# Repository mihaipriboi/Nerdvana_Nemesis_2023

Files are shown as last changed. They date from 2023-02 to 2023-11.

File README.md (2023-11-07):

<center><h1> Nerdvana Nemesis 2023 </center>

## Table of Contents
* [Photos](#team-image)
  * [Team](#team-image)
  * [Robot](#robot-image)
* [Performance Video](#video)
* [Mobility Management](#mobility-management)
  * [Powertrain](#powertrain-mechanical)
    * [Drivetrain](#drivetrain-mechanical)
    * [Motor](#motor-mechanical)
    * [Motor Driver](#motor-driver-mechanical)
  * [Steering](#steering-mechanical)
    * [Servo Motor](#servo-motor)
  * [Chassis](#chassis-mechanical)
* [Power and Sense Management](#power-and-sense-management)
  * [Li-Po Battery](#li-po-battery)
  * [Teensy 4.1](#teensy-4.1)
  * [LIDAR](#lidar-sensor)
  * [IMU](#imu-sensor)
  * [Pixycam 2.1](#pixy-cam-2.1)
  * [Voltage Regulator](#voltage-regulator-(L7805CV))
  * [Circuit Diagram](#circuit-diagram)
* [Code for each component](#code-for-each-component)
  * [Drive Motor](#drive-motor-code)
  * [Servo Motor](#servo-motor-code)
  * [Camera](#camera-code)
  * [LIDAR](#lidar-code)
    * [Python Data Visualization](#python-data-visualization)
  * [IMU](#gyro-sensor-code)
  * [SD Card](#sd-card-code)
* [Obstacle Management](#obstacle-management)
  * [Qualification Round](#quali-management)
  * [Final Round](#final-management)
* [Randomizer](#randomizer)
* [Resources](#resources)
  * [3D Models](#3d-models-resources)
  * [Images](#images-resources)

### Team: Priboi Mihai, Onișoru Antonia, Bălan Teodor 
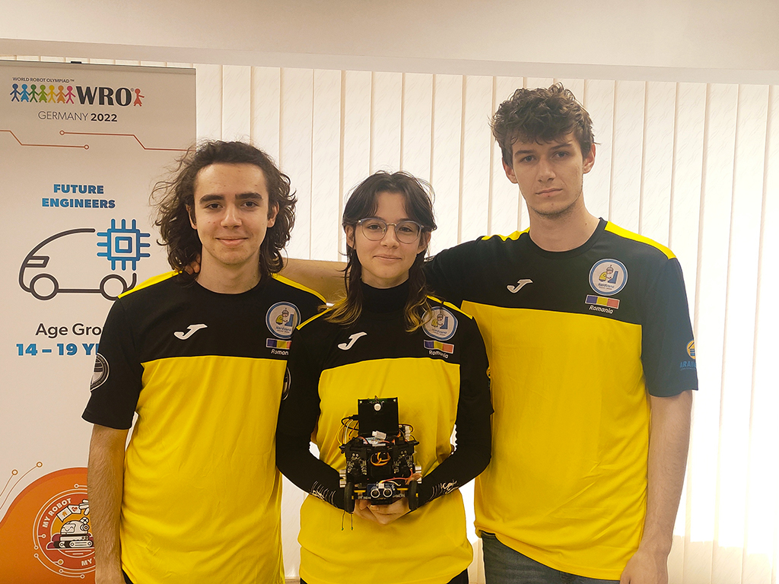
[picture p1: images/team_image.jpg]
Team
  

## Photos of our robot Paula Mia (**P**retty **A**wesome **U**ltra **L**ocomotion **A**utonomous **M**apping **I**ntelligence **A**ugmentation) 

|  |  | 
| :--: | :--: |
| *Front* | *Back* |
|  |  | 
| *Left* | *Right* |
|  |  | 
| *Top* | *Bottom* |

<br>

## Our video of the robot on [Youtube](https://youtu.be/1fn3-xTy-k4) 

<br>

# Mobility Management 
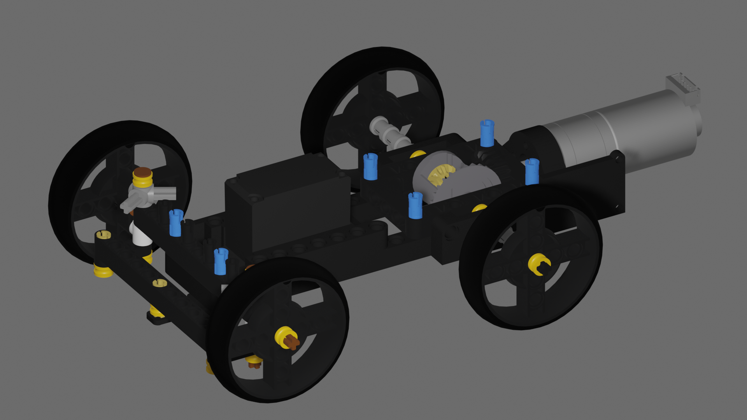
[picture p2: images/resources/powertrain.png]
Powertrain


## Powertrain 

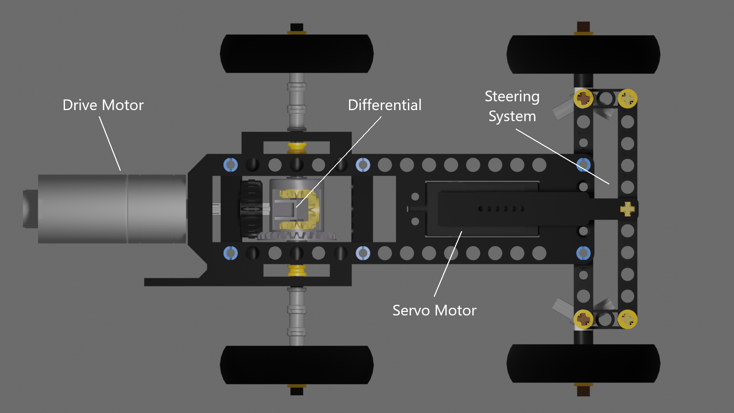
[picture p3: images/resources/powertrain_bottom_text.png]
Powertrain - Bottom View


### Drivetrain 

After reflecting on our experience from last year's competition, where we utilized a rear-wheel drive (RWD) with a differential, we opted for an all-wheel drive (AWD) system for this year's national event. We were motivated to switch because the RWD struggled with steering due to the lack of power in the front wheels. Moreover, an AWD system ensures a more even distribution of power.

However, after deciding to incorporate a LIDAR sensor, we found it essential to mount the sensor low to improve its accuracy. Given its considerable size, and the space constraints for the front differential and driveshaft—further challenged by our decision to place the servo lower to make room for the LIDAR—we ultimately returned to the RWD configuration.

To minimize friction and thereby reduce speed loss, we avoided using 3D-printed components for the moving parts in the drivetrain. Instead, we utilized Lego pieces, which are molded with high precision and therefore have a very low friction coefficient. The 3D-printed parts were reserved for the chassis and for mounting the electronic components onto the Lego structure.

### Motor 

Following an evaluation of different motors, we settled on a geared DC motor that comes with a magnetic encoder. This motor was selected for its lightweight and compact design, which stands out among others with comparable output. Additionally, the magnetic encoder offers greater precision than its optical counterpart. We secured the motor to the chassis using screws.

**Specifications:**
- Voltage: < 7V
- Gear Ratio: 1:20
- Speed: 400 ± 13% rpm
- Torque: 0.4 ± kg·cm
- Weight: 67.4g

Where to buy the motor: https://www.adafruit.com/product/4416

To connect the motor's axle to a Lego-compatible axle, we created a custom 3D-printed adapter.

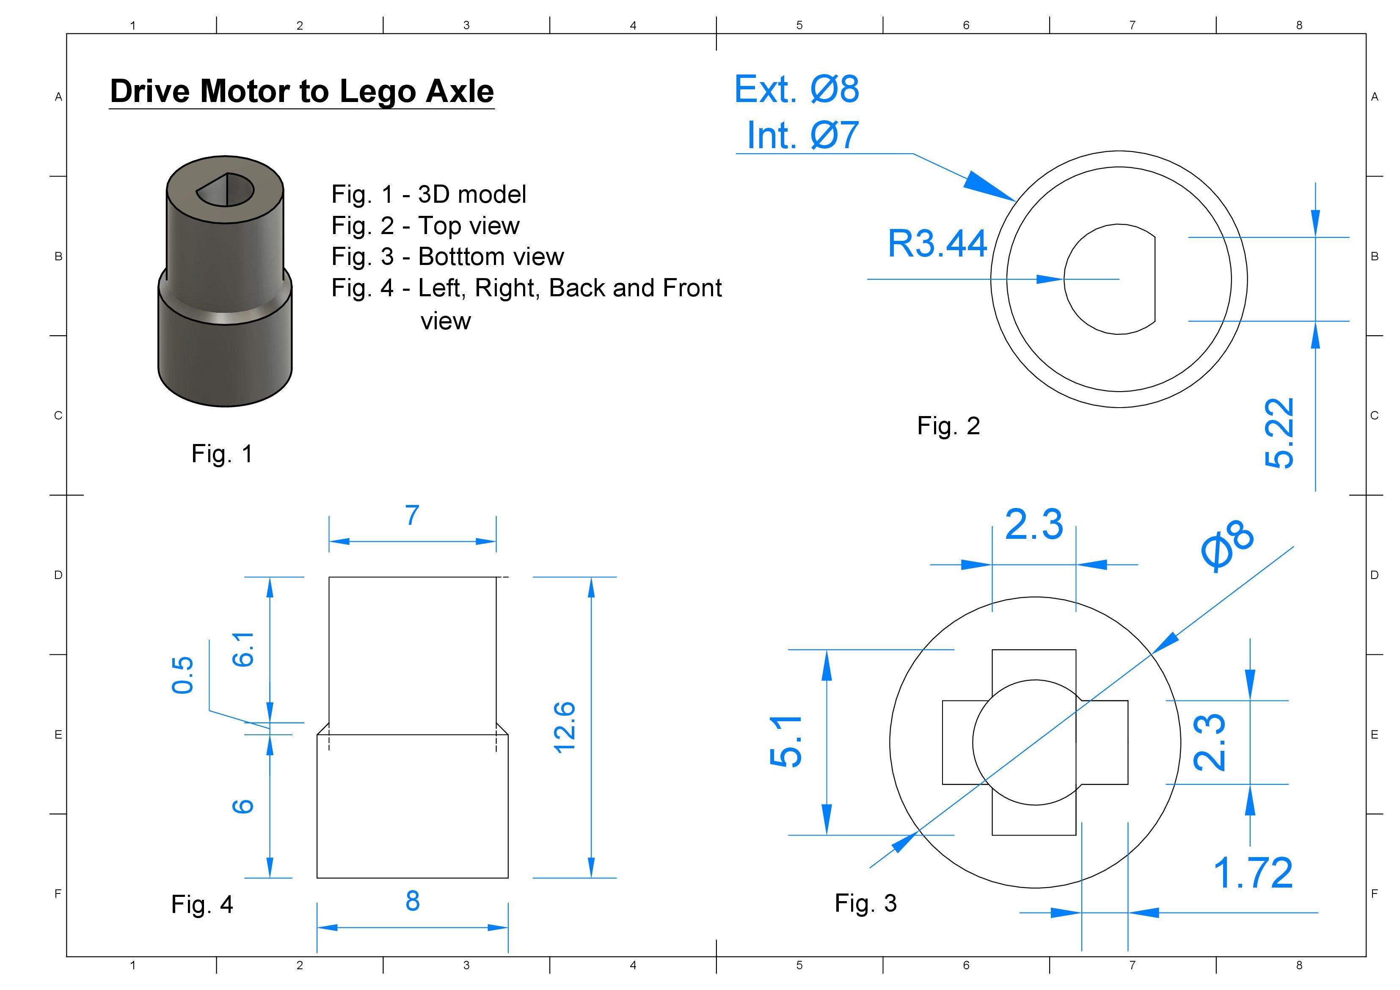
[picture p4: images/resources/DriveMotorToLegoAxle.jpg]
Gearmotor to axle - 3D Model Gearmotor to axle 3D piece


### Motor Driver 
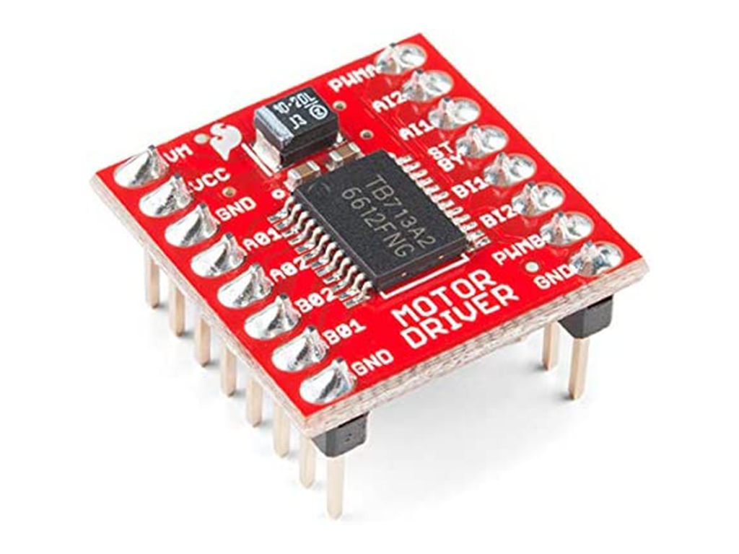
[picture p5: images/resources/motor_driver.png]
Motor driver


To control the speed of the drive motor, we utilized a SparkFun Dual TB6612FNG motor driver.

Where to buy the motor driver: https://www.sparkfun.com/products/14450

## Steering 

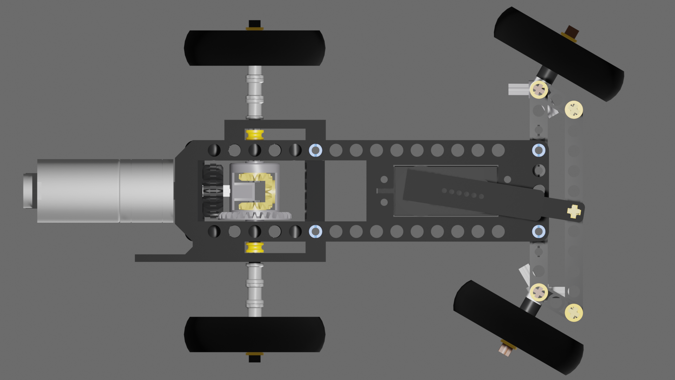
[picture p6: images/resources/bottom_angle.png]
Powertrain - Angled Bottom View


After experimenting with various steering mechanisms such as Ackermann steering and bell-crank steering, we assessed their advantages and drawbacks. Ultimately, we chose a straightforward steering system consisting of a parallelogram linkage. This decision was made because the alternative systems were either too large or too complex to implement effectively. Our selected mechanism is simple, light, and compact, providing a satisfactory steering angle. While it does not adhere to the Ackermann steering geometry, our tests showed that for our robot's small size and light weight, this omission was not critically significant.

### Servo Motor 
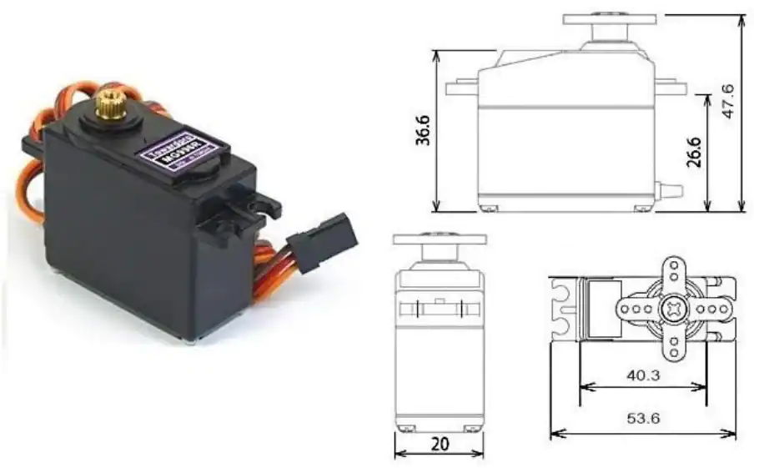
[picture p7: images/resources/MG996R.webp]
MG996R Servo


For steering, we selected the MG996R servo motor, favoring it for its high torque and swift response.

**Specifications:**
- Weight: 55g
- Stall torque: 9.4 kg/cm (4.8v)
- Operating speed: 0.17 s/60 degree (4.8v)
- Rotation angle: 180 degree

Where to buy the servo motor: https://www.sigmanortec.ro/servomotor-mg996r-180-13kg

To connect the servo motor to the steering system, we fashioned a custom 3D-printed adapter. Given the dynamic geometry of the system, the connector couldn't be a single rigid piece because its length needed to be adjustable according to the wheel positions. Thus, we designed a two-part beam: the larger piece attaches to the servo and the smaller piece to the steering mechanism. The smaller piece slides into the larger one, permitting the beam's length to vary. We introduced a slight space between the two components to ensure smooth movement, while also ensuring that a significant portion of the smaller piece remains within the larger one to avoid disconnection or bending.

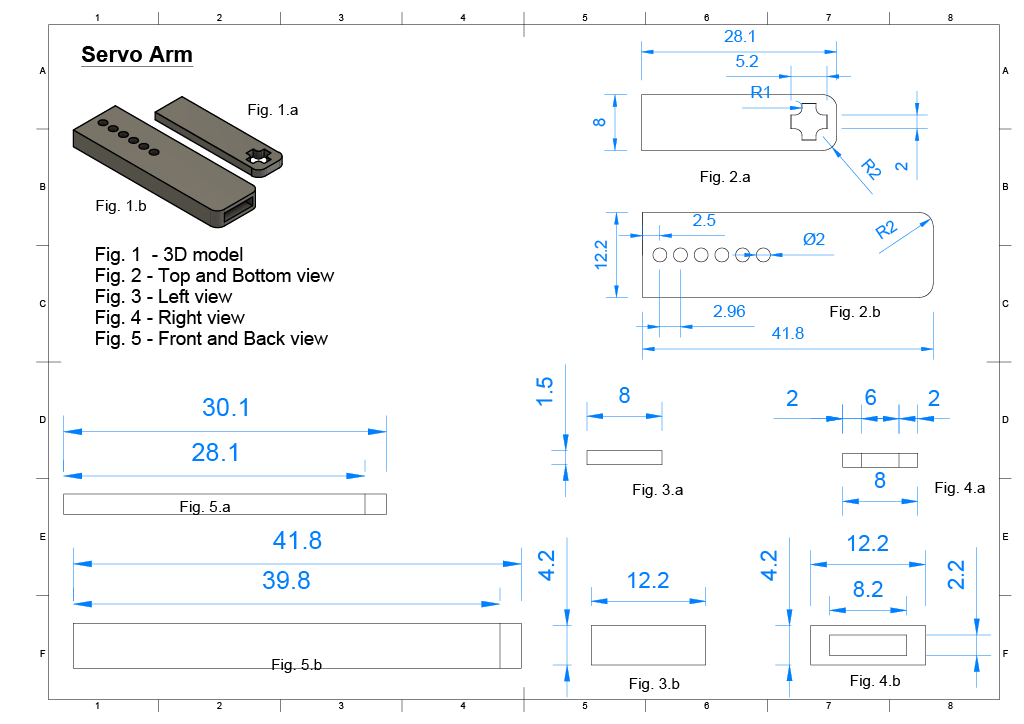
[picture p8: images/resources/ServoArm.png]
Servo Arm - 3D Model Servo Arm


## Chassis 

Our initial prototypes utilized Lego pieces to assemble all components, which simplified testing and design modifications. Once we finalized the design, we transitioned to a custom 3D-printed chassis for assembling the mechanical parts. This choice proved to be superior, resulting in a lighter and more compact structure that offered greater design flexibility compared to the Lego-based framework. The chassis accommodates the drivetrain and steering mechanism and includes designated mounts for securing the drive motor and servo motor.

Incorporating a LIDAR system necessitated maintaining all components, except for the LIDAR itself, below a certain height (approximately 8 cm, slightly less than the wall height) to ensure an unobstructed field of view for the sensor. Consequently, we had to extend the robot's length more than preferred, but this was an essential compromise. The drive motor extends out from the back of the robot, while the servo motor is centrally positioned directly beneath the LIDAR. Due to spatial constraints preventing the servo motor from being placed higher, we relinquished the all-wheel drive in favor of an alternative configuration. The gyroscope sensor is also mounted on the chassis, positioned near the drive motor.

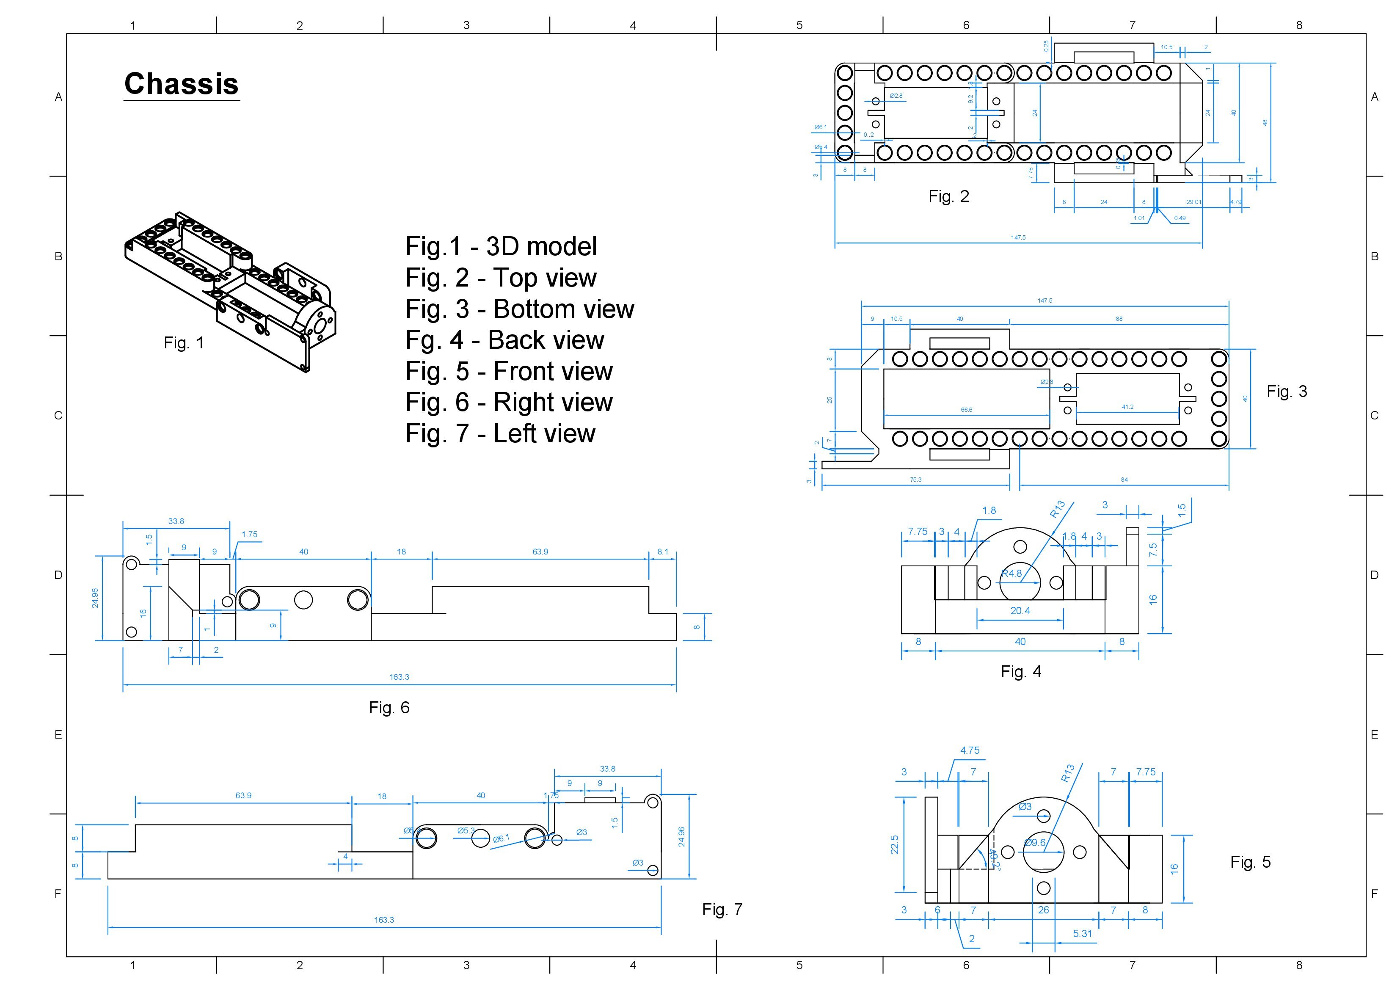
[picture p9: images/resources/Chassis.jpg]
Chassis - 3D Model


# Power and Sense Management 

### Li-Po Battery 
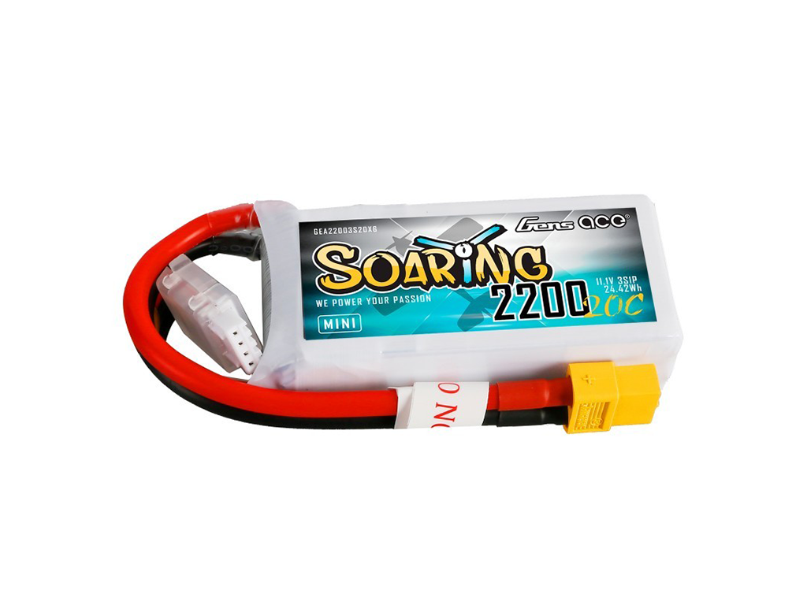
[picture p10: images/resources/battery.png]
Li-Po Battery


Last year, we powered our robot with a 6-pack of AA Nickel-Metal Hydride (NiMH) batteries, which provided approximately 7.2V and 2000mAh but weighed around 650g. With our goal of building a smaller and lighter robot, we recognized the need for a different power source. We chose a Lithium Polymer (Li-Po) battery for its lighter weight, more compact size, and quicker charging capabilities. The specific model we selected is the *LiPo GENS ACE Soaring* (7.4V, 2200mAh, 20C). Switching to this battery reduced the weight of our power pack from 650g to 100g, almost halving the robot's weight. Moreover, the battery is more than twice as small in terms of volume.

Where to buy the battery: https://www.sierra.ro/Acumulator-LiPo-GENS-ACE-Soaring-7-4-V--2200-mA--20C-p11141p.html

The battery is mounted using a custom 3D-printed holder, which is secured to the chassis.

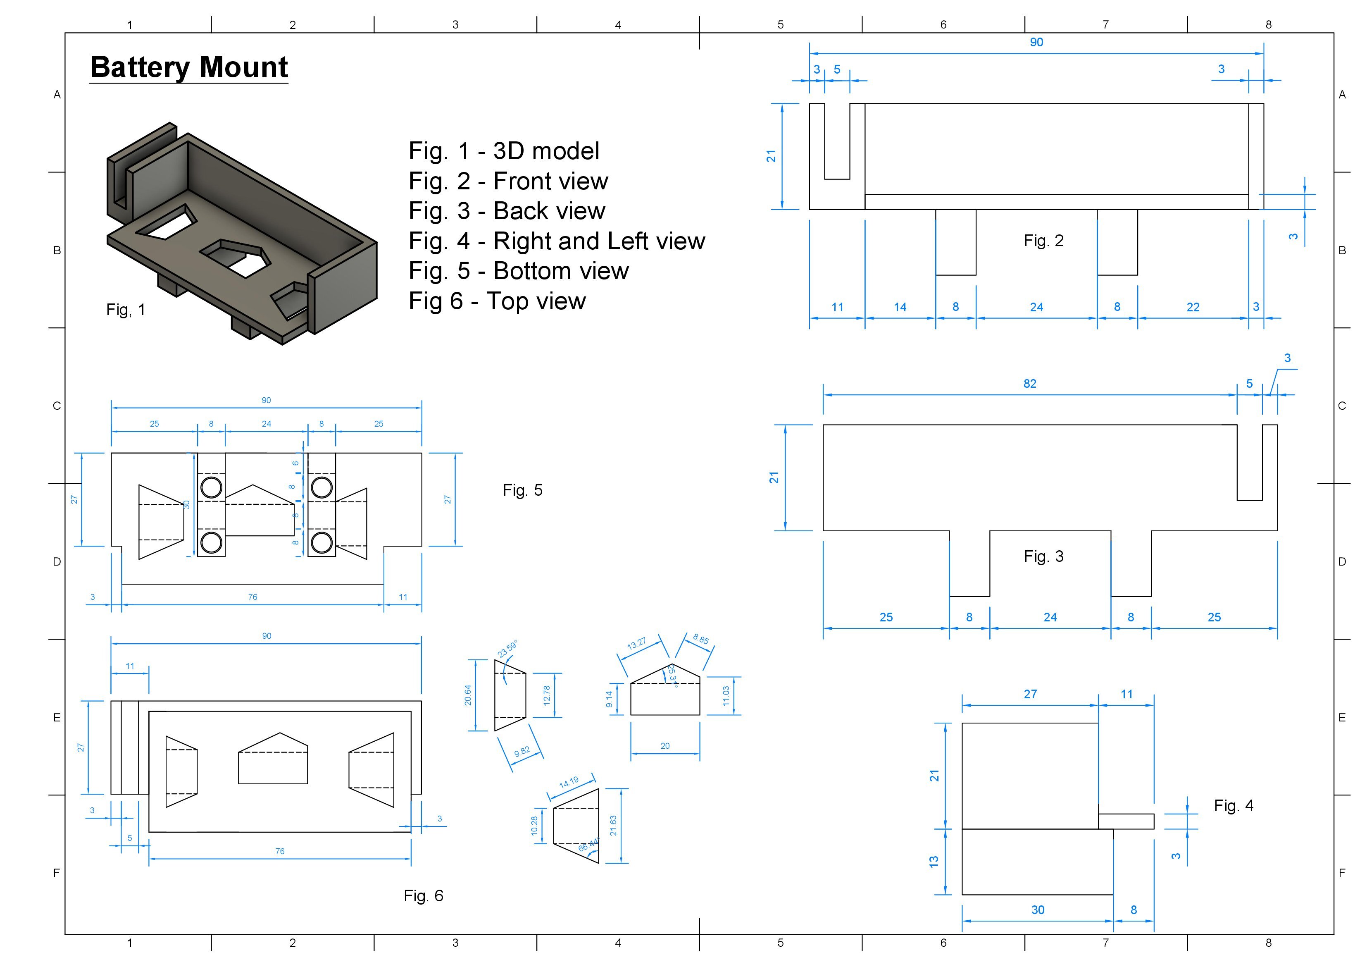
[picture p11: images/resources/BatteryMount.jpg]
Battery Mount - 3D Model


### Teensy 4.1 
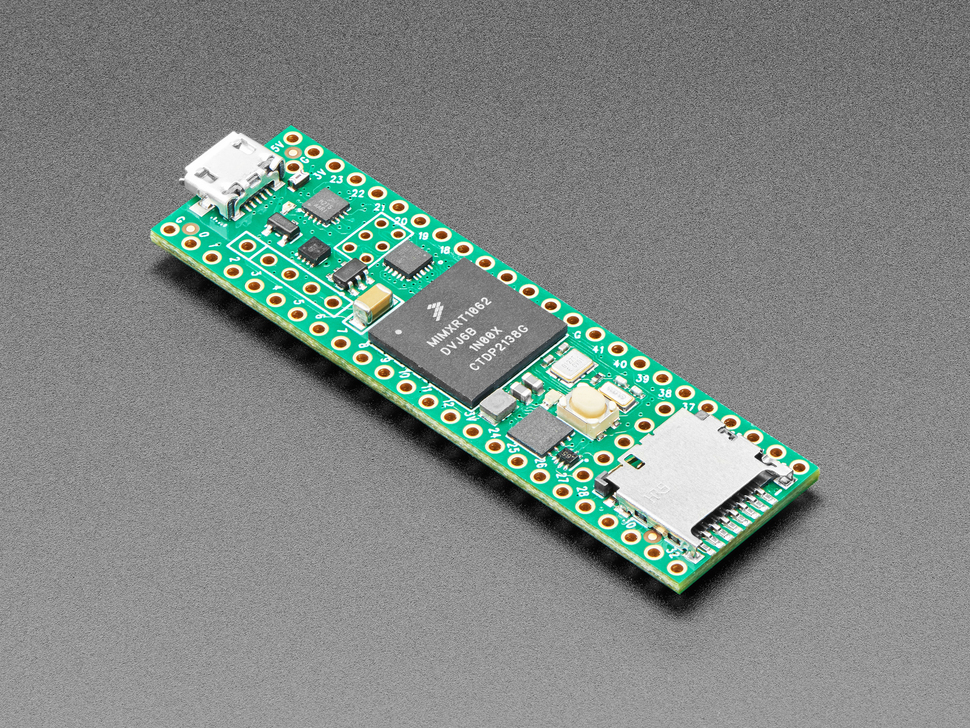
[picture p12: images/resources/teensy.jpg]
Teensy 4.1 Teensy 4.1


At WRO2022 Future Engineers, we used a Raspberry Pi 3B+ in conjunction with an Arduino Uno Every through a serial connection. The Raspberry Pi was tasked with processing images from the camera, whereas the Arduino was dedicated to controlling the motors and collecting sensor data. This method, however, was not optimal. The processing speed of the Raspberry Pi fell short of our requirements, the serial link between the two boards was not as quick as necessary, and it also carried the risk of data loss.

Following the international competition in Dortmund, we discovered the Pixycam 2.1, a camera equipped with its own processing capabilities that can directly connect to an Arduino or other microcontrollers. With the Pixycam 2.1, we were able to remove the Raspberry Pi, thereby enhancing our robot's speed. We also upgraded from the Arduino Uno Every to a Teensy 4.1, which boasts much faster processing power.

| Specification | Arduino Nano Evey | Teensy 4.1 |
| :--: | :--: | :--: |
| Clock Speed | 20MHz | 600 MHz |
| CPU Flash Memory | 48 KB | 8 Mbytes |
| CPU RAM | 6 KB | 1 MB |
| Digital I/O Pins | 20 | 42 |
| PWM Pins | 7 | 14 |
| UART | 1 | 6 |
| SPI | 1 | 3 |
| I2C | 1 | 3 |

Where to buy the Teensy 4.1: https://www.pjrc.com/store/teensy41.html

The Teensy, mounted on a prototype board, is secured to the chassis with a custom 3D-printed holder.

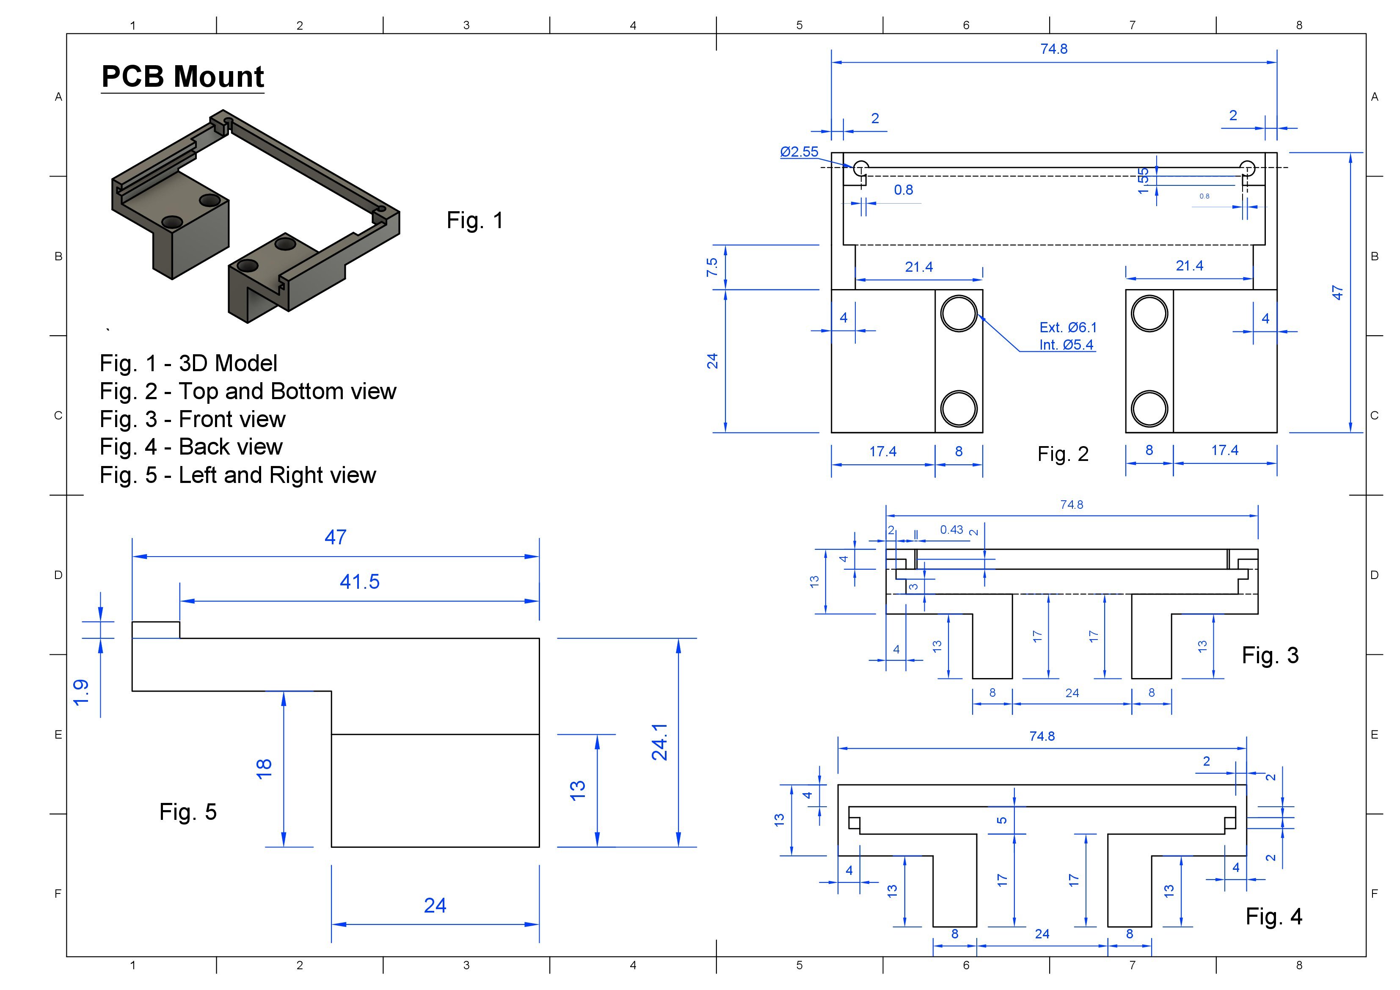
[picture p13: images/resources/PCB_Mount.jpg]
PCB Mount - 3D Model


### LIDAR 
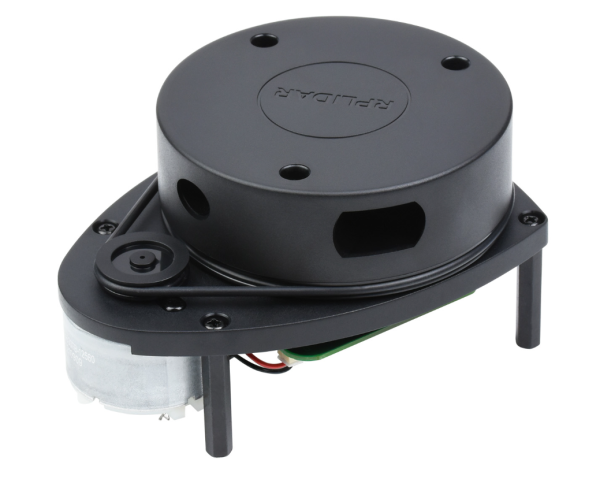
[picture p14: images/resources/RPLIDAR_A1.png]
RPLIDAR A1


The LIDAR A1 sensor is a crucial component of our robot. It provides the robot with a 360° view of its surroundings, allowing it to detect obstacles and avoid collisions. We selected the RPLIDAR A1, which is a low-cost LIDAR system that offers a 360° scan at a frequency of 10Hz. The sensor is equipped with a 2D laser scanner that can detect objects up to 8 meters away. The sensor is wired to the Teensy 4.1 via the SDA and SCL pins.

In the lead-up to the World Robot Olympiad (WRO) 2022, an iterative process of solution development was undertaken, aiming to resolve the persistent challenge of precise robot localization and obstacle detection under variable environmental conditions. The trials encompassed the deployment of both ultrasonic and infrared sensors. However, these sensors exhibited limitations in terms of angular sensitivity and dependability, influenced by the robot's orientation, which impeded their effectiveness for consistent environmental navigation and recognition tasks.

Where to buy the RPLIDAR A1: https://www.adafruit.com/product/4010

The LIDAR is secured to the chassis with custom 3D-printed holders on each leg.

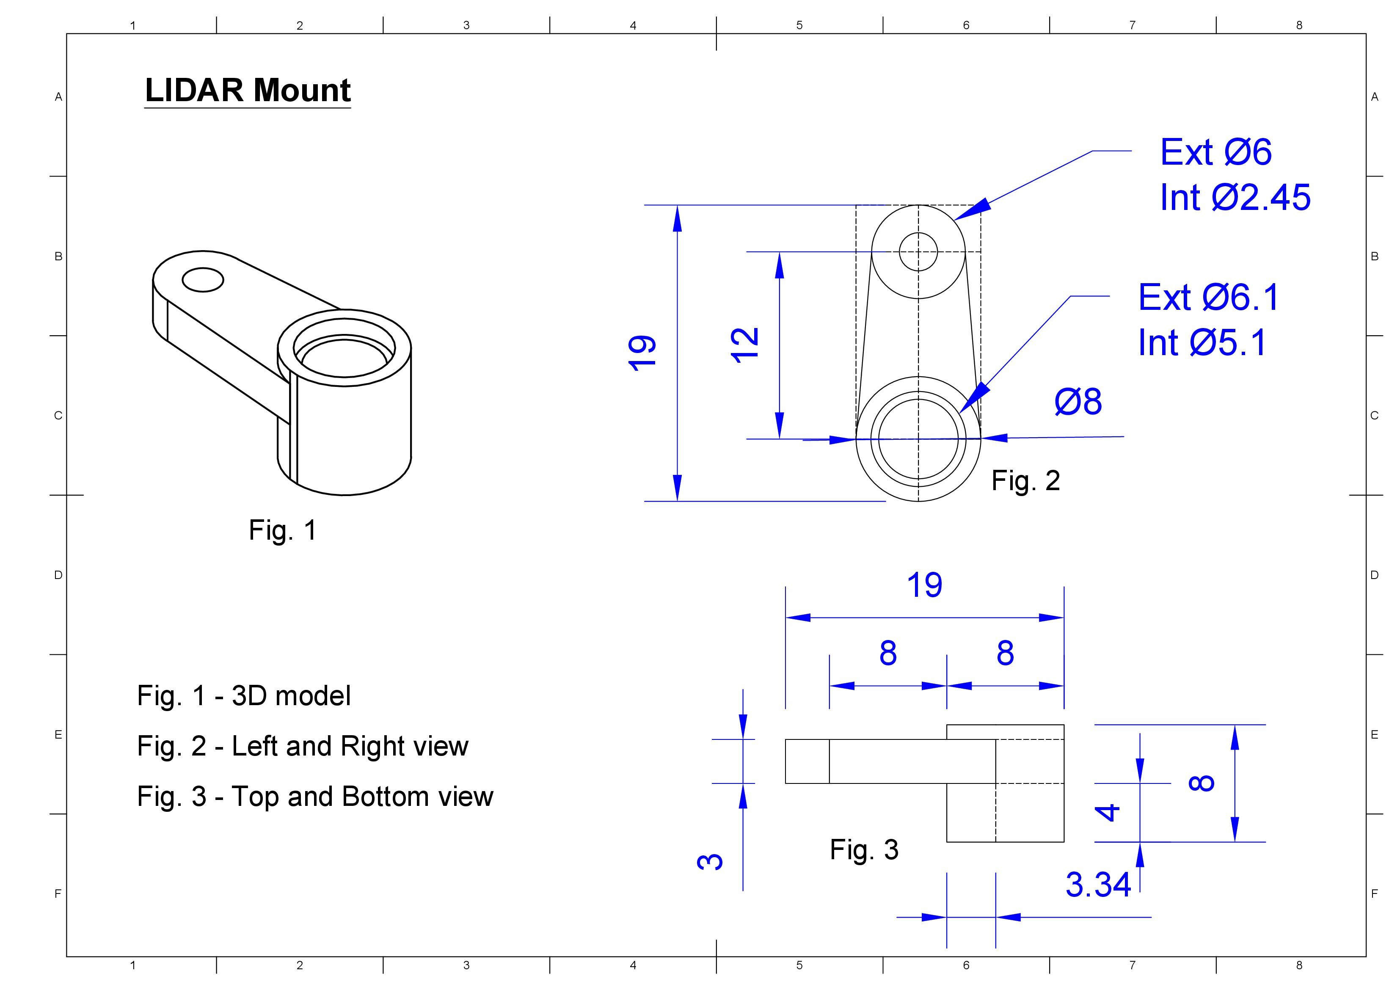
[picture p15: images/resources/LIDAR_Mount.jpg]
LIDAR Mount - 3D Model


### IMU 
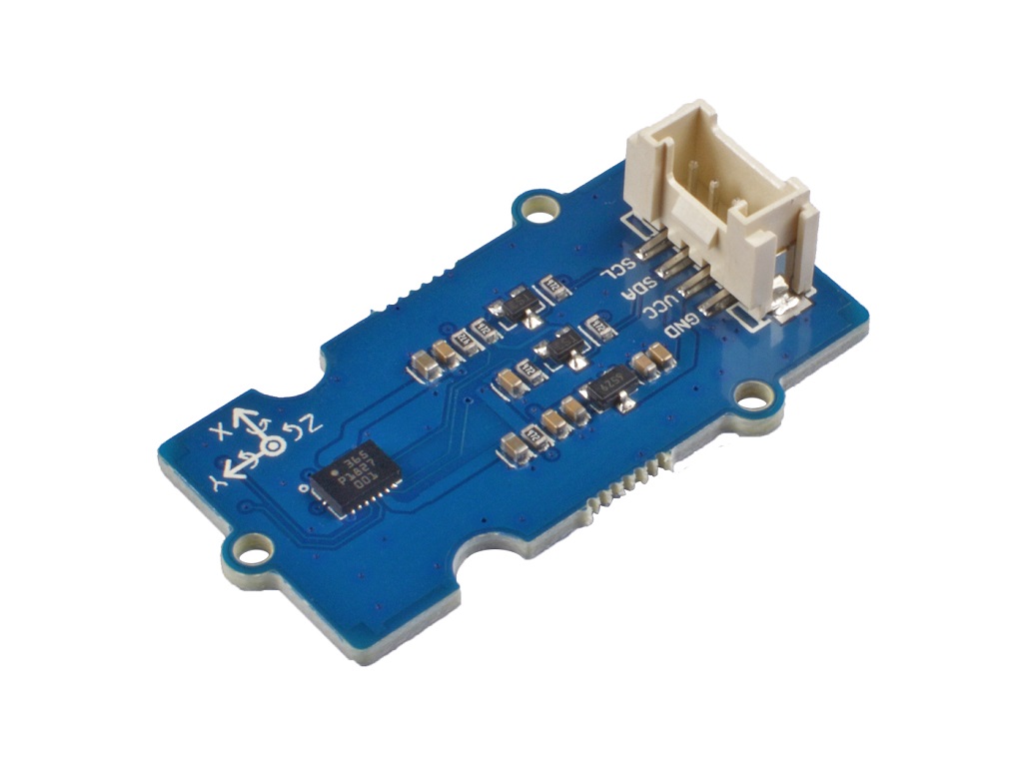
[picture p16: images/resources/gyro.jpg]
IMU Sensor - BMI088


One importat aspect that helps the roboy navigate is the inertial measurement unit (IMU). After using the MPU6050 last year, we decided to upgrade to a better IMU. This sensor is based on BOSCH BMI088, which is a high-performance IMU with high vibration suppression. While the IMU measure the angular velocity and the acceleration of the robot, we only use the angular velocity to calculate the angle of the robot. The IMU is wired to the SDA and SCL pins on the teensy.

**Specifications:**
- Gyroscope range: ±2000°/s
- Accelerometer range: ±24g

Where to buy the gyro sensor: https://www.seeedstudio.com/Grove-6-Axis-Accelerometer-Gyroscope-BMI088.html

### Pixycam 2.1 
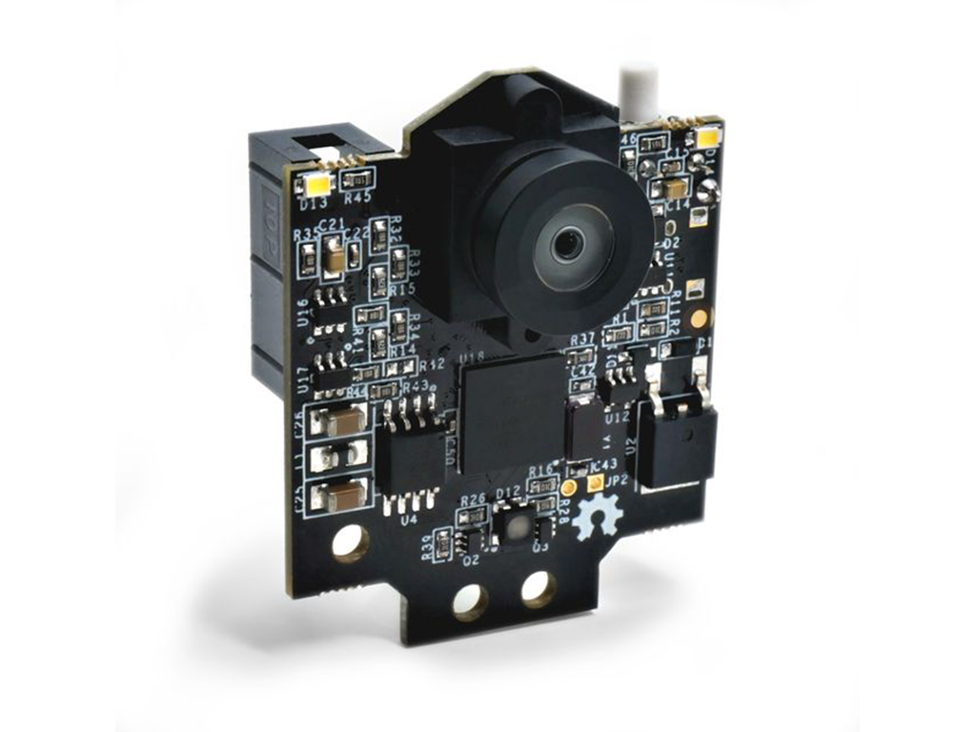
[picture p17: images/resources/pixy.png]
Pixycam 2.1


Last year, one of our main challenges was the slow speed of the camera feed. We were utilizing a Raspberry Pi equipped with a PiCam V2. The delay was primarily due to the need to run a cube recognition machine learning algorithm on the Raspberry Pi itself, which limited the processed image feed to around 15 frames per second. This not only reduced the camera's efficiency but also slowed down the processing of other tasks on the Raspberry Pi.

To address this, we switched to the Pixycam 2.1, which offers several significant benefits: it possesses its own processing unit, thus preventing any lag in the rest of the system; it comes with a professionally developed machine learning algorithm for object detection and tracking, which performs reliably; and it can directly interface with an Arduino or another microcontroller, eliminating the need for a Raspberry Pi and so increasing the frequency of the readings.

Together with the Teensy 4.1, the camera delivers readings at approximately 60 frames per second, a limit we've set ourselves. Additionally, the camera's operation doesn't impact the performance of other sensors, allowing us to take full advantage of their capabilities.

Where to buy the PixyCam 2.1: https://www.robotshop.com/products/charmed-labs-pixy2-robot-vision-image-sensor-lego-rbc

The Pixycam 2.1 is mounted on the chassis with a custom 3D-printed holder.

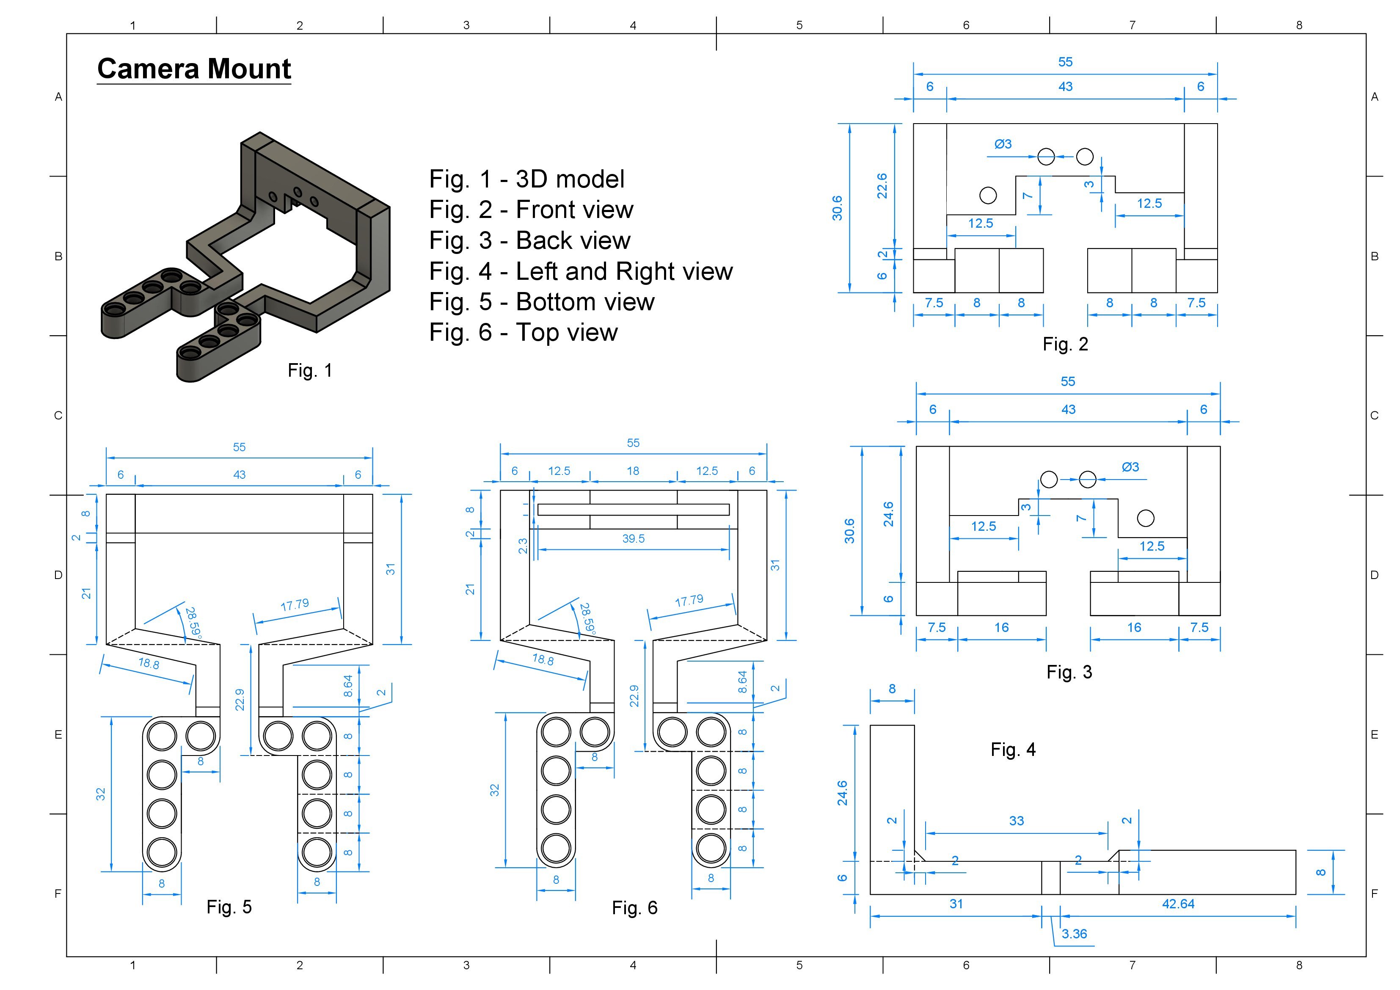
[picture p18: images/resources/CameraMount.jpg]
Pixycam Mount - 3D Model


### Voltage regulator 
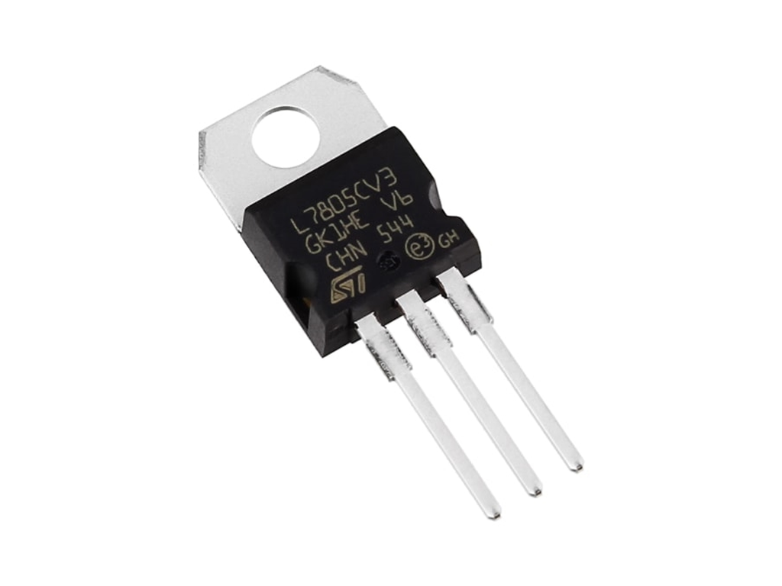
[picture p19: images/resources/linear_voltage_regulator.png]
Voltage regulator (L7805CV)


To provide the Teensy 4.1 with the required 5V, we needed to decrease the output from the 7.4V battery, which can reach up to 8.4V when fully charged. We employed a linear voltage regulator, the L7805CV, capable of converting input voltages below 35V down to a steady 5V.

For the drive motor, which we want to operate at higher speeds, we use a separate voltage regulator, the L7806CV, to step down the battery's 7.4V to 6V. This approach allows us to extract more speed from the motor while maintaining consistent performance across different battery charge levels.

Where to buy the 5V voltage regulator: https://ro.mouser.com/ProductDetail/STMicroelectronics/L7805CV?qs=9NrABl3fj%2FqplZAHiYUxWg%3D%3D

Where to buy the 6V voltage regulator: https://ro.mouser.com/ProductDetail/STMicroelectronics/L7806CV?qs=K4DpzJ20gDEC%252BHE13eVUwg%3D%3D

### Circuit diagram 
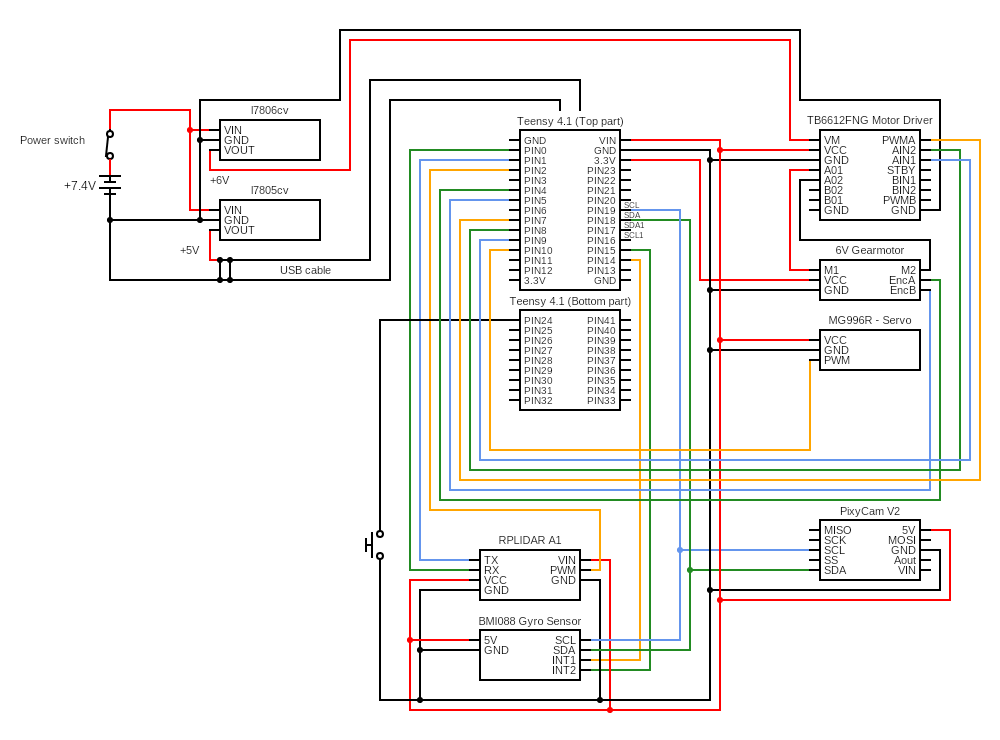
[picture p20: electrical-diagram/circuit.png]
Circuit diagram


<br>

# Code for each component 

## Drive Motor 

The motor driver can be directly managed with a single PWM pin that adjusts the motor's speed and two digital pins designated for determining the motor's rotation direction. Consequently, the use of any external library for motor manipulation was unnecessary.

We devised two functions within our control system: one to modify the motor's velocity and another to halt it effectively, incorporating a braking feature. To achieve this, we convert the desired speed from our established scale of -100 to +100 to the PWM equivalent of 0 to 255. The motor's direction is then adjusted according to the sign of the input value.

```ino
void motor_start(int speed) {
  speed = -speed;  
  int out = abs(speed) * 2.55; // Convert speed to PWM value (0 to 255)
  if(speed >= 0) { // Forward direction
    digitalWrite(AIN1, HIGH);
    digitalWrite(AIN2, LOW);
  }
  else { // Reverse direction
    digitalWrite(AIN1, LOW);
    digitalWrite(AIN2, HIGH);
  }
  analogWrite(PWM1, out);

  Serial << "speed: " << speed << "\n";
}

void motor_stop() {
  motor_start(-10); 
}
```

However, for the encoder, we required a specialized library to handle the more complex signal processing. The library we use for interfacing with the encoder is called *Encoder.h*.

The encoder operates with a straightforward function that we found easy to comprehend and program. The constant with which we multiply the encoder's output value was determined empirically through multiple tests with varying distances. This calibration process allowed us to accurately convert the encoder's readings into centimeters.

```ino
long read_motor_encoder() {
  return (0.01285) * (double)myEnc.read();
}
```

## Servo Motor 

For controlling the servo motor, we utilize the *Servo.h* library, which provides the necessary functions to manage the servo's movements. Initially, we configure the servo by establishing its range, defining the maximum and minimum angles it can achieve in both directions. This ensures that we can accurately position the servo within its operational limits.

```ino
// Servo
void servo_setup() {
  servo.attach(SERVO_PIN, 1400, 1611);
  move_servo(0);
  delay(50);
}
```

The function *move_servo* makes the servo to rotate a specific angle, given by the parameter _angle_. If the angle is negativ the motor will rotate to the left, and if is pozitiv the motor will rotate to right. This way 0 is going to be the position, in which the wheels are straight. Also, the values we are giving the motor need to be between -1 and 1, so we use a clamp function to limit the value we are going to give the motor to roatate to.

```ino
void move_servo(double angle) {
  angle = clamp(angle + servo_correction, -1, 1);

  double angle_deg = 90 + angle * 90.0;  // Convert angle to degrees (0 to 180)
  angle_deg = clamp(angle_deg, 0, 180);
  servo.write(angle_deg);
}
```

## Camera 

Now that we finished to implement the functions we need to make the robot move and steer, we have to make him see the cubes and move according to them. The library we used for the camera is _Pixy2I2C.h_. The I2C address must be configured in the _Pixy2I2C.h_ library.

```ino
void camera_setup(bool debug) {
  if (debug) Serial.println(F("Camera starting..."));
  //display_print("Cam err!");
  pixy.init(0x54);
  if (debug) Serial.println(F("Camera ok!"));

  pixy.getResolution();
  image_w = pixy.frameWidth;
  image_h = pixy.frameHeight;
  // Serial << image_w << " " << image_h << '\n';
}
```

In order to read the inputs from the camera, we have some methods from the Pixy2I2C class.

```ino
pixy.ccc.blocks[i].m_signature
// The signature number of the detected object
// For us, 1 is for red, and 2 is for green
pixy.ccc.blocks[i].m_x
// The x location of the center of the detected object (0 to 316)
pixy.ccc.blocks[i].m_y
// The y location of the center of the detected object (0 to 208)
pixy.ccc.blocks[i].m_width
// The width of the detected object (1 to 316)
pixy.ccc.blocks[i].m_height
// The height of the detected object (1 to 208)
pixy.ccc.blocks[i].m_indez
// The tracking index of the block
```

For the camera we made a function in which we are reading the color of the cube in front of us.

```ino
void read_camera(bool debug) {
  if (millis() - last_camera_read >= camera_interval) {
    pixy.ccc.getBlocks();

    if(pixy.ccc.numBlocks < 1)
      cube_color = 0;
    else
      cube_color = sig_to_col[pixy.ccc.blocks[0].m_signature];

    last_camera_read = millis();
  }
}
```

## LIDAR 

Extracting data from the LIDAR involves processing a continuous stream via Serial1. The lidarRead() function reads bytes one at a time, confirming the correct sequence before storing them in a buffer. Once enough data is gathered, it's processed to inform the robot's navigation. If the buffer is full, the data is saved for later use and the buffer is reset for new data. This method ensures the robot receives reliable information for obstacle detection and avoidance.

```ino
void lidarRead() {
    if (!Serial1.available()) {
        return;
    }
    byte current_byte = Serial1.read();
    if (lidar_buff_ptr == 0) {
        if ((current_byte >> 4) != 0xA) {
            return;
        }
    } else if (lidar_buff_ptr == 1) {
        if ((current_byte >> 4) == 0xA) {
            lidar_buff_ptr = 0;
        } else if ((current_byte >> 4) != 0x5) {
            lidar_buff_ptr = 0;
            return;
        }
    }

    lidar_buff[lidar_buff_ptr++] = current_byte;

    if (lidar_buff_ptr == 4) {
        lidarProcessingData();
    }

    if (lidar_buff_ptr == 84) {
        memcpy(lidar_old_buff, lidar_buff, 84);
        lidar_buff_ptr = 0;
    }
}
```

The lidarProcessingData() function interprets raw LIDAR data to map out the robot's surroundings. It calculates the starting angle of the scan and then iterates over the data to determine distances and angles for various points. These values are then adjusted for the robot's current orientation, converted into X and Y coordinates, and filtered to ignore any out-of-range readings. If the readings are valid, they're processed further to assist the robot in navigation and obstacle avoidance.

```ino
void lidarProcessingData() {

    double start_angle = (((uint16_t)(lidar_buff[3] & 0b01111111) << 8) ^ lidar_buff[2]) / 64.;
    double old_start_angle = (((uint16_t)(lidar_old_buff[3] & 0b01111111) << 8) ^ lidar_old_buff[2]) / 64.;

    for (int i = 0; i < 16; ++i) {
        byte* cabin = lidar_old_buff + 5 * i + 4;
        
        d0[0] = getDiffAngle(((cabin[0] & 0b11) << 4) ^ (cabin[4] & 0b1111));
        d0[1] = getDiffAngle(((cabin[2] & 0b11) << 4) ^ (cabin[4] >> 4));

        for (int i = 0; i < 2; ++i) {
            distance[i] = ((uint16_t)cabin[2 * i + 1] << 6) ^ (cabin[2 * i] >> 2);
        }

        for (int j = 0; j < 2; ++j) {
            int k = 2 * i + 1 + j;
            double angle = old_start_angle + angleDiff(old_start_angle, start_angle) / 32 * k;
            if (angle >= 360) {
                angle -= 360;
            } else if(angle < 0) {
              angle = angle + 360;
            }

            double x, y;

            float gx_angle = fmod((double)(angle + (double)gx - current_angle), 360.0);

            y = -distance[j] * cos(radians(gx_angle));
            x = -distance[j] * sin(radians(gx_angle));

            if(distance[j] > 5 && distance[j] < 4000) {
              lidarProcessPoint(Angle(distance[j], gx_angle), Point(x, y));
            }
        }
    }
}
```

The *calculate_linear_regression_segment* function performs a linear regression analysis on a set of data points from LIDAR readings to determine the linear path that best fits the trajectory of an observed barrier. It computes the line's gradient and intercept, pinpoints the coordinates for the beginning and end of the trajectory, and ascertains the barrier's direction in relation to the robot's orientation. Additionally, this function measures the shortest distance from the robot to the barrier.

Another part of the code accumulates data points into a 'current line' array if they are incrementally consistent in distance and direction with the previously recorded point. When this collection reaches a certain size, or there is a notable shift in the data points' position or angle, it initiates the aforementioned linear regression analysis on the gathered segment. Should the barrier be located at a substantial distance, this detected range is then updated. Special conditions within the function are also set to recognize the contours of a cube, modifying the cube's recorded distances as needed when certain parameters are fulfilled.

```ino
void calculate_linear_regression_segment(Point& start, Point& end, double& dist, int& dir) {  
  if(current_line_size < 2) return; // Not enough points for regression
  
  double x_start = INFINITY, x_end = -INFINITY;
  double x_sum = 0, y_sum = 0, x2_sum = 0, xy_sum = 0;
  for(int i = 0; i < current_line_size; ++i) {
    x_sum += current_line[i].x;
    y_sum += current_line[i].y;
    x2_sum += current_line[i].x * current_line[i].x;
    xy_sum += current_line[i].x * current_line[i].y;

    if(current_line[i].x < x_start) x_start = current_line[i].x;
    if(current_line[i].x > x_end) x_end = current_line[i].x;
  }

  double m, c;

  if(current_line_size * x2_sum - x_sum * x_sum == 0) m = INF;
  else m = (current_line_size * xy_sum - x_sum * y_sum) / (current_line_size * x2_sum - x_sum * x_sum);
  
  c = (y_sum - m * x_sum) / current_line_size;

  start.x = x_start;
  start.y = m * x_start + c;
  
  end.x = x_end;
  end.y = m * x_end + c;

  dist = abs(c) / sqrt(1 + m * m);

  if(abs(m) < 0.4) {
    if((start.y + end.y) / 2 < 0) 
      dir = BACK;
    else 
      dir = FRONT;
  } else {
    if((start.x + end.x) / 2 < 0)  {
      dir = LEFT; 
    }
    else {
      dir = RIGHT;
    }
  }
  slopes[dir] = m;
}

void lidarProcessPoint(Angle angl, Point p) {
  double ang, dist;
  ang = angl.ang;
  dist = angl.dist;

  if(abs(dist - old_dist) < 10 && min(abs(ang - old_ang), 360 - abs(ang - old_ang)) < 1.5) {
    current_line[current_line_size++] = p;
  } else {
      if(current_line_size > calculate_threshold(old_dist)) {
        Point start, end;
        double wall_d;
        int wall_dir;

        calculate_linear_regression_segment(start, end, wall_d, wall_dir);

        if(wall_d > 50) {
          old_wall_dist[wall_dir] = wall_dist[wall_dir];
          wall_dist[wall_dir] = wall_d;
          if(wall_dir == FRONT && (wall_dist[FRONT] + wall_dist[BACK]) < 2800) {
            wall_dist[BACK] = 3050 - wall_d;
          }
          wall_updated[wall_dir] = true;
        }

      }
      else if(current_line_size > 2 && (abs(dist - old_dist) > 20 || 
      abs(ang - old_ang) > 5) && (old_ang > 120 && old_ang < 240) &&
       old_dist < 1000 && old_dist > 100 && (wall_dist[BACK] < 1500 ||
        wall_dist[FRONT] > 1400)) {
        xa = current_line[current_line_size / 2].x;
        ya = current_line[current_line_size / 2].y;

        if(xa && ya && wall_dist[side_wall]) {
          double na = ya - slopes[side_wall] * xa;
          dist_to_cube = (-1) * na / sqrt(slopes[side_wall] * slopes[side_wall] + 1);
          //left
          if(dist_to_cube && !last_dist_to_cube && cube_color && abs(wall_dist[side_wall] + direction * dist_to_cube) < 850) { 
            last_dist_to_cube = dist_to_cube;
            last_cube_y = wall_dist[BACK] + ya;
            if(last_cube_y > 2000)
              last_cube_y = 2000;
            if(last_cube_y < 1000)
              last_cube_y = 1000;
          } 
        }
      }
      current_line_size = 0;
      current_line[current_line_size++] = p;
  }
  old_dist = dist;
  old_ang = ang;
}
```

We found that the number of points defining a line decreases with distance in LIDAR data. To predict this variation, we applied a polynomial model that helps improve our detection and mapping accuracy.

```ino
import numpy as np

data = np.loadtxt('data.csv', delimiter=',')

distances = data[:, 0]
points = data[:, 1]

coefficients = np.polyfit(distances, points, 2)

a, b, c = coefficients

print("Best fit parameters: a =", a, "b =", b, "c =", c)

def polynomial_function(D):
    return a * D**2 + b * D + c

distance = 100
estimated_points = polynomial_function(distance)
print("Estimated points at distance", distance, "cm:", estimated_points)

```

```ino
double calculate_threshold(double distance) {
  distance /= 10.0; 
  double a = 0.0010947040728267199;
  double b = -0.46574727812407213;
  double c = 56.010728111461475;
  double points = a * distance * distance + b * distance + c;
  double threshold = max(7.0, points);  // Ensure threshold is at least 7
  threshold = min(20, threshold);
  return threshold;
}
```

The gyro sensor's measurement of the robot's rotation angle is essential for precise spatial positioning. This angle adjusts the lidar data to reflect true distances, accounting for changes in position and orientation. Neglecting this leads to mapping inaccuracies, hence, rotation compensation is critical for precise navigation.

### Python Data Visualization 

To simplify the configuration process for the LIDAR sensor, we developed a Python script that graphically represents the sensor's data. This script takes the wall segments detected by the LIDAR, illustrates them in a chart, and annotates each with the measured distance from the robot. Below, you'll find a sample visualization generated by this program.

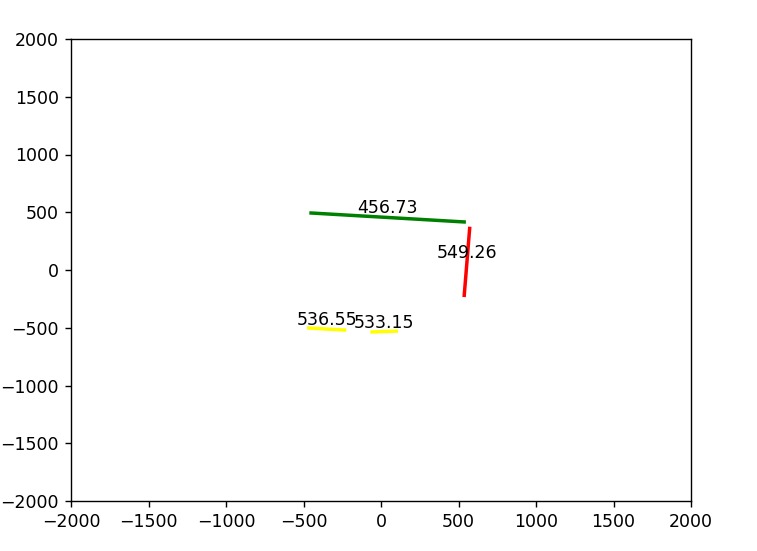
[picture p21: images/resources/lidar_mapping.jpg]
LIDAR Python Mapping


```py
from cmath import cos
from math import radians, sin, sqrt
import math
import matplotlib.pyplot as plt
from collections import deque
import random
import time
import numpy as np
import serial

# Arduino setup
arduino = serial.Serial(port='COM9', baudrate=115200, timeout=.1)

# Create a fixed-length deque of length 50 to store the data points
data_points = deque(maxlen=600000)

# Create an empty plot
fig, ax = plt.subplots()

# Set the x-axis and y-axis limits
ax.set_xlim(-2000, 2000)
ax.set_ylim(-2000, 2000)

# Create a scatter plot to visualize the data points
scatter = ax.scatter([], [])

last_update_time = time.time()

update_interval = 0.5

data = arduino.readline().decode().strip()
old_dist, old_ang = map(float, data.split())

line_counter = 0
colorLines = ['black', 'red', 'blue', 'green', 'yellow', 'orange', 'purple', 'pink', 'brown', 'gray']
colorVec = []

saveLine = []
lines = []
cubes = []

m_left = 0

def calculate_linear_regression_segment(points):
    x, y = points[:, 0], points[:, 1]
    A = np.vstack([x, np.ones_like(x)]).T
    m, c = np.linalg.lstsq(A, y, rcond=None)[0]
    
    # Calculate endpoints of the segment
    x_start = x.min()
    y_start = m * x_start + c
    
    x_end = x.max()
    y_end = m * x_end + c

    dist = abs(c) / np.sqrt(1 + m**2)

    return x_start, y_start, x_end, y_end, m, dist

def plot_segment_with_coefficient(ax, points, order):
    global m_left
    x_start, y_start, x_end, y_end, m, dist = calculate_linear_regression_segment(points)

    color = 'black'
    #black not determined
    #red right
    #blue left
    #green up
    #yellow down

    if(abs(m) < 1): # horizontal line
      if((y_start + y_end) / 2 < 0):
        color = 'yellow'
      else:
        color = 'green'
    else:
      if (x_start + x_end) / 2 < 0:
        color = 'blue'
        m_left = m
      else:
        color = 'red'
       
    ax.plot([x_start, x_end], [y_start, y_end], color=color, linewidth=2)
    # get distnace from origin to the line
    
    ax.text((x_start + x_end) / 2, (y_start + y_end) / 2, f'{round(float(dist), 2)}', 
            horizontalalignment='center', verticalalignment='bottom')

def calculate_threshold(distance):
    distance = distance / 10
    a = 0.0010947040728267199
    b = -0.46574727812407213
    c = 56.010728111461475
    points = a * distance**2 + b * distance + c
    threshold = max(14, points)  # Ensure threshold is at least 14
    threshold = min(20, points)
    return threshold

# Main loop to continuously read and update data
while True:
    data = arduino.readline().decode().strip()
    if data:
        dist, ang = map(float, data.split())
        point_y = -1 * dist * cos(radians(ang));
        point_x = -1 * dist * sin(radians(ang));

        if(old_ang <= 360 and ang >= 0 and old_ang > ang):
           if(len(lines)):  

            for line in ax.lines:
              line.remove()
            for text in ax.texts:
              text.remove()

            order = 0
            for line in lines:
              plot_segment_with_coefficient(ax, line, order)
              order += 1

            if m_left:
              for cube in cubes:
                x1, y1 = cube[0]
                b = y1 - m_left * x1
                y_line = m_left * np.array([x1, x1 - 100]) + b  # x1+10 is just an example, you can choose other values
                dist = -1 * b / sqrt(m_left * m_left + 1)
                ax.plot([x1, x1 - 100], y_line, color="black", linewidth=2)
                ax.text((x1 + x1 - 100) / 2, (y1) / 2, f'{round(float(dist), 2)}', 
                  horizontalalignment='center', verticalalignment='bottom')

            cubes.clear()

            lines = []
            cubes = []
            
            line_counter = 0
            colorVec = []
            pointCnt = 0

            plt.pause(0.00001)
            
        if(abs(dist - old_dist) < 10 and min(abs(ang - old_ang), 360 - abs(ang - old_ang)) < 1.5):
            saveLine.append((point_x, point_y))
        else:
            if(len(saveLine) > calculate_threshold(old_dist)):

              lines.append(np.array(saveLine));
              # save line is a list of tuples

              # data_points.extend(saveLine)
              # colorVec.extend([colorLines[line_counter]] * len(saveLine))
              line_counter += 1
            elif(len(saveLine) > 2 and (abs(dist - old_dist) > 20 or abs(ang - old_ang) > 5) and (old_ang > 130 and old_ang < 240) and old_dist < 800):
               cubes.append(np.array(saveLine));
               data_points.extend(saveLine)
            saveLine.clear()
            saveLine.append((point_x, point_y))

        old_dist = dist
        old_ang = ang

# Show the plot
plt.show()

```

## IMU 

To utilize the gyro sensor, we needed to include the _BMI088.h_ library. During initialization, we allocate a 10-second window to measure the sensor's drift, allowing us to refine the robot's angular readings for greater precision. Additionally, we configure the sensor's output data rate to 400Hz and set the bandwidth to 47Hz. The bandwidth determines the frequency of data sampling by the sensor; a higher bandwidth yields more precise data at the cost of increased power consumption. We also designate pin 15 as an input and attach an interrupt to it, enabling us to capture data from the sensor as soon as it becomes available.

```ino
void gyro_setup(bool debug) {
  int status = accel.begin();
  status = accel.setOdr(Bmi088Accel::ODR_200HZ_BW_80HZ);
  status = accel.pinModeInt1(Bmi088Accel::PUSH_PULL,Bmi088Accel::ACTIVE_HIGH);
  status = accel.mapDrdyInt1(true);

  status = gyro.begin();

  status = gyro.setOdr(Bmi088Gyro::ODR_400HZ_BW_47HZ);
  status = gyro.pinModeInt3(Bmi088Gyro::PUSH_PULL,Bmi088Gyro::ACTIVE_HIGH);
  status = gyro.mapDrdyInt3(true);

  pinMode(15,INPUT);
  attachInterrupt(15,gyro_drdy,RISING);  

  if(status < 0) {
    if(debug) Serial << "BMI Initialization Error!  error: " << status << "\n";
    //init_error = init_gyro_error = true;
  }
  else  {
    // Gyro drift calculation
    if(debug) Serial.println("Starting gyro drift calculation...");

    gx = 0;
    gy = 0;
    gz = 0;

    gyro_last_read_time = millis();

    double start_time = millis();
    while(millis() - start_time < DRIFT_TEST_TIME * 1000) {
      gyro.readSensor();  
      double read_time = millis();
      gx += (gyro.getGyroX_rads() * (read_time - gyro_last_read_time) * 0.001);
      // gy += (bmi.getGyroY_rads() * (read_time - gyro_last_read_time) * 0.001);
      // gz += (bmi.getGyroZ_rads() * (read_time - gyro_last_read_time) * 0.001);

      gyro_last_read_time = read_time;
    }

    drifts_x = gx / DRIFT_TEST_TIME;
    // drifts_y = gy / DRIFT_TEST_TIME;
    // drifts_z = gz / DRIFT_TEST_TIME;

    if(debug) Serial.print("Drift test done!\nx: ");
    if(debug) Serial.print(drifts_x, 6);
    if(debug) Serial.print("   y: ");
    if(debug) Serial.print(drifts_y, 6);
    if(debug) Serial.print("   z: ");
    if(debug) Serial.println(drifts_z, 6);
  }
  // Gyro value reset
  gx = 0;
  gy = 0;
  gz = 0;

  gyro_last_read_time = millis();
}
```

Within the *read_gyro* function, we're retrieving data from the gyro sensor and adjusting it to account for any detected drift, enhancing the accuracy of the readings. Since the gyro provides data in radians, a conversion to degrees is necessary for our application. We're focusing solely on the rotation around the x-axis, hence we only compute the *gx* value, which represents the robot's angular rotation in degrees on that specific axis.

```ino
void read_gyro(bool debug) {
  //delta_start = millis();
  if(gyro_flag) {
    gyro_flag = false;
    cnt1++;
    gyro.readSensor();   
    double read_time = millis();

    gx += ((gyro.getGyroX_rads() - drifts_x) * (read_time - gyro_last_read_time) * 0.001) * 180.0 / PI;
    //gy -= ((bmi.getGyroY_rads() - drifts_y) * (read_time - gyro_last_read_time) * 0.001) * 180.0 / PI;
    //gz -= ((bmi.getGyroZ_rads() - drifts_z) * (read_time - gyro_last_read_time) * 0.001) * 180.0 / PI;

    gyro_last_read_time = read_time;

    //delta_gyro = millis() - delta_start;
    if(debug) Serial << "Gyro: gx: " << gx << "    gy: " << gy << "    gz: " << gz << "\n";

    if(debug) {
      Serial.print("Gyro: gx: ");
      Serial.print(gx);
      Serial.print(" gy: ");
      Serial.print(gy);
      Serial.print(" gz: ");
      Serial.println(gz);
    }
  }
}
```

## SD Card 

Utilizing the Teensy 4.1, we encounter the limitation of not being able to monitor the robot's sensor data in real time. Nonetheless, it's essential for us to access this information. Our solution is straightforward: we record all the data the robot collects onto an SD card, taking advantage of the built-in SD card slot on the Teensy board. To facilitate this, we implemented the *SD.h* and *SPI.h* libraries.

To store data onto the SD card, we crafted several functions. The function named *file_print* records data continuously without line breaks, whereas *file_println* appends a newline after each entry. Both functions accept a String parameter, which represents the data being saved.

Additionally, we utilize a function named *writeSD* in our current setup. Its operation is simple: we concatenate data to a string variable, and upon completing this, the entire string is written to the SD card.

```ino
/// SD card functions

void SD_setup() {
  if (!SD.begin(chipSelect)) {
    Serial.println("Card failed, or not present!");
    //init_sd_error = true;
  }
  else {
    Serial.println("Card present!");

    // SD.remove("datalog.txt");

    int i = 0;
    do {
      char aux[100];
      itoa(i, aux, 10);

      memset(sd_filename, 0, sizeof(sd_filename));

      strcat(sd_filename, "datalog_");
      strcat(sd_filename, aux);
      strcat(sd_filename, ".csv");

      i++;
    } while(SD.exists(sd_filename));

    if(debug) Serial.print("Using filename: ");
    if(debug) Serial.println(sd_filename);
  }
}

void file_print(String s) {
  File data_file = SD.open(sd_filename, FILE_WRITE);
  if(data_file) {
    data_file.print(s);
    data_file.close();
  }
}

void file_println(String s) {
  File data_file = SD.open(sd_filename, FILE_WRITE);
  if(data_file) {
    data_file.println(s);
    data_file.close();
  }
}

void writeSD(int aux, int aux2, int aux3, int aux4) {
  data_string += "time " + String(millis()) + " , "; 
  data_string += "left " + String(wall_dist[LEFT]) +  " , right " + String(wall_dist[RIGHT]) + " , FRONT " + String(wall_dist[FRONT]) + " , ";
  data_string += "pd_case: " + String(pid_case) + " , ";
  data_string += "case: " + String(CASE) + ", ";
  data_string += "pd err: " + String(pid_error) + " ,gx " + String(gx)+ ", ang:" + String(current_angle)+'\n';

  if(aux)
    data_string += "aux: " + String(aux) + ", ";
  if(aux2)
    data_string += "aux1: " + String(aux2) + ", ";
  if(aux3)
    data_string += "aux2: " + String(aux3) + ", ";
  if(aux4)
    data_string += "aux3: " + String(aux4) + ", ";

  if(millis() - sd_last_write_time > 1000) {
    file_println(data_string);
    data_string = "";
    sd_last_write_time = millis();  
  }
}
``` 

<br>

# Obstacle Management 

## Qualification Round 

For the qualifying round, we set up a basic switch-case system to guide our robot. This system tells the robot what to do next, depending on where it is. The robot knows where it is by counting how many times it has turned.

We use three main switch cases: *SECTION*, *ROTATE*, and *STOP*.

In the *SECTION* case, the robot just moves straight. It uses a special tool (PID controller) with a gyro sensor to stay on a straight line. If it gets too close to the walls, it uses another tool (PID controller) with a LIDAR sensor to keep the right distance from the walls. When it comes to a corner, it changes to the *ROTATE* case.

```ino
case SECTION: {
  if(wall_dist[FRONT] > 0 && wall_dist[FRONT] < 500) {
    writeSD(1, -1, -1, -1);
    pid_case = 0;
    current_angle += direction * 90;
    turns++;
    last_rotate = millis();
    CASE = ROTATE;
  }
  else if(abs(pid_error) <= 0.15 || abs(wall_dist[RIGHT] - wall_dist[LEFT]) > 1200) {
    pid_case = 1;
    pid_error_gyro = (current_angle - gx) * kp_gyro + (pid_error_gyro - pid_last_error_gyro) * kd_gyro;
    pid_last_error_gyro = pid_error_gyro;

    move_servo(pid_error_gyro); 
  }
  else {
    if(millis() - last_time_pid > 10 && wall_dist[LEFT] && wall_dist[RIGHT] && abs(wall_dist[RIGHT] - wall_dist[LEFT]) < 1200) {
      pid_case = 2;
      move_servo(pid_error); 
      pid_error = (wall_dist[RIGHT] - wall_dist[LEFT]) * kp + (pid_error - pid_last_error) * kd;
      pid_last_error = pid_error;
      last_time_pid = millis();
    }
  }
  break;
}
```

The *ROTATE* case is for when the robot needs to turn at corners. It decides which way to turn based on which side has more space. If the robot has turned 12 times, it changes to the *STOP* case.

```ino
case ROTATE: {
  if((wall_dist[RIGHT] - wall_dist[LEFT]) < 1200 && abs(current_angle - gx) < 5 && millis() - last_rotate >= 1000) {
    if(turns >= 12) 
      CASE = STOP;
    else
      CASE = SECTION;
  } else {
    pid_error_gyro = (current_angle - gx) * kp_gyro + (pid_error_gyro - pid_last_error_gyro) * kd_gyro;
    pid_last_error_gyro = pid_error_gyro;

    move_servo(pid_error_gyro); 
  } 
  break;
}
```

The *STOP* case is for when the robot finishes the course. It tells the robot to stop moving.

```ino
case STOP: {
  delay(500);
  move_servo(-1);
  motor_start(-5);
  Serial.println("Stop case");
  writeSD(-1, -1, -1, -1);
  delay(100000);
  break;
}
```

## Final Round 

For the final round resolution, we adopted a three-tiered modular approach to achieve greater precision and fluidity. The first module is designed for navigating through the current section, the second for detecting and evading any immediate cubes, and the third for executing rotations and setting up for the following section.

The initial segment serves as the core switch-case structure within our code, where we continuously monitor for any cubes to avoid or for cues to initiate a rotation in preparation for the upcoming section. Should neither of these conditions arise, the robot is programmed to maintain a direct trajectory through the segment, ensuring uninterrupted progress.

```ino
case SECTION: {
  if(turn_ok && wall_dist[FRONT] && wall_dist[FRONT] < 700  && millis() - last_rotate > rotate_timeout) {
    turns++;
    last_rotate = millis();
    last_cube_color = 0;
    last_dist_to_cube = 0;
    flag = 0;
    cube_section_cnt = 0;
    if (wall_dist[side_wall] > 550)
      CASE = ROTATE;
    else
      current_angle += direction * 90;   
  } else if (last_dist_to_cube && cube_color != last_cube_color && cube_color != 0 && wall_dist[BACK] < 1800) {
    move_servo(cube_color * 1);

    if (cube_color == GREEN) {
      if(direction == 1)
        goal_distance = 250 + (wall_dist[side_wall] - 230) / 6;
      else
        goal_distance = 850 - (1000 - wall_dist[side_wall]) / 6;
    } else {
      if(direction == 1)
        goal_distance = 770 - (1000 - wall_dist[side_wall]) / 5;
      else
        goal_distance = 270 + (wall_dist[side_wall] - 200) / 5;
    }

    last_cube_color = cube_color;
    cube_section_cnt++;

    if(turns == 3) {
      final_cube_color = last_cube_color;
      final_cube_pos = cube_section_cnt;
      final_cube_turn = turns;
    } 
    if(turns == 4) {
      if(last_cube_y < 1700) {
        final_cube_color = last_cube_color;
        final_cube_pos = cube_section_cnt;
        final_cube_turn = turns;
      }
    }
    
    CASE = AVOID_CUBE;
  } else {

    if(millis() - last_turn_ok > rotate_timeout && (wall_dist[BACK] > 1850 || (wall_dist[LEFT] + wall_dist[RIGHT]) > 1200) && !turn_ok) {
      turn_ok = 1;
      last_turn_ok = millis();
    }
    pid_error_gyro = ((current_angle) - gx) * kp_gyro + (pid_error_gyro - pid_last_error_gyro) * kd_gyro;
    pid_last_error_gyro = pid_error_gyro;

    move_servo(pid_error_gyro);
  }
  break;
}
```

The *AVOID_CUBE* module is responsible for detecting and avoiding any cubes that may be present in the robot's path. It utilizes the LIDAR sensor to determine the cube's position and color, and then it calculates the shortest distance to the cube. The robot then adjusts its trajectory to avoid the cube, and once it has passed it, it goes to the *PASS CUBE* module.

In the *PASS CUBE* module, the robot moves straight until it has passed the cube. Once it has done so, it goes back to the *SECTION* module.

```ino
case AVOID_CUBE:
{
  if (last_cube_color == GREEN && ((wall_dist[side_wall] < goal_distance && direction == 1) || (wall_dist[side_wall] > goal_distance && direction == -1))  || 
        last_cube_color == RED && ((wall_dist[side_wall] > goal_distance && direction == 1) || (wall_dist[side_wall] < goal_distance && direction == -1)) && 
          (wall_dist[LEFT] + wall_dist[RIGHT]) > 800) {
    CASE = PASS_CUBE;
  } else {
    pid_error_gyro = ((current_angle + last_cube_color * 55) - gx) * kp_gyro + (pid_error_gyro - pid_last_error_gyro) * kd_gyro;
    pid_last_error_gyro = pid_error_gyro;

    move_servo(pid_error_gyro);
  }
  break;
}

case PASS_CUBE:
{
  if (wall_dist[BACK] > last_cube_y + 200 && (wall_dist[FRONT] + wall_dist[BACK]) < 3400) {
    last_dist_to_cube = 0;
    if(final_cube_color == 1 && final_cube_turn % 4 == turns % 4 && turns > 5 && final_cube_pos == cube_section_cnt)
      CASE = PASS_LAST_CUBE;
    else
      CASE = SECTION;
  } else {
    pid_error_gyro = (current_angle - gx) * kp_gyro + (pid_error_gyro - pid_last_error_gyro) * kd_gyro;
    pid_last_error_gyro = pid_error_gyro;

    move_servo(pid_error_gyro);
  }
  break;
}
```

The *ROTATE* module is designed to pivot the robot 90 degrees towards the next section. It employs a PD controller in conjunction with a gyro sensor to execute the rotation. However, if the robot is close to the inside wall, it will perform a 270-degree turn in the opposite direction rather than a 90-degree one. This ensures the robot has ample space to maneuver before approaching the next section, thereby avoiding any cubes.

```ino
case ROTATE:
{
  if (abs((current_angle - direction * 270) - gx) < 5) {
    current_angle -= direction * 270;
    last_rotate = millis();
    CASE = SECTION;
  } else if ((wall_dist[side_wall] > 500 || wall_dist[FRONT] > 450) && (wall_dist[side_wall] > 450 || wall_dist[FRONT] > 250) && flag == 0) {
    ang = myacos((wall_dist[FRONT] - 450) / sqrt((wall_dist[FRONT] - 450) * (wall_dist[FRONT] - 450) + (wall_dist[side_wall] - 500) * (wall_dist[side_wall] - 500)));

    pid_error_gyro = ((current_angle - direction * ang) - gx) * kp_gyro + (pid_error_gyro - pid_last_error_gyro) * kd_gyro;
    pid_last_error_gyro = pid_error_gyro;

    move_servo(pid_error_gyro);
  } else {
    flag = 1;
    pid_error_gyro = ((current_angle - direction * 270) - gx) * kp_gyro + (pid_error_gyro - pid_last_error_gyro) * kd_gyro;
    pid_last_error_gyro = pid_error_gyro;

    move_servo(pid_error_gyro);
  }
  break;
}
```

The *PASS_LAST_CUBE* module is designed to rotate the robot and change its direction after 2 laps, in case the last cube has the color red.

```ino
case PASS_LAST_CUBE: {
  if(wall_dist[FRONT] && wall_dist[FRONT] < 500) {
    current_angle -= 180;
    direction *= -1;
    if(side_wall == LEFT)
      side_wall = RIGHT;
    else
      side_wall = LEFT;
    last_rotate = millis();
    last_cube_color = 0;
    last_dist_to_cube = 0;
    flag = 0;
    cube_section_cnt = 0;
    turns++;
    CASE = SECTION;
  } else {
    pid_error_gyro = (current_angle - gx) * kp_gyro + (pid_error_gyro - pid_last_error_gyro) * kd_gyro;
    pid_last_error_gyro = pid_error_gyro;

    move_servo(pid_error_gyro);
  }
  break;
}
```

THe *STOP* module is designed to stop the robot after it has completed the course.

```ino
case STOP:
  {
    lidarMotorWrite(0);
    move_servo(0);
    motor_start(-10);
    Serial.println("Stop case");
    break;
  }
```

<br>

# Randomizer 

To ensure the robot's ability to adapt to any course, we developed a randomizer that generates a random sequence of colors and positions for the cubes. You can find this web application at the following link: https://nerdvana.ro/wro-fe/

<br>

# Resources 

## 3D Models 
<li> DC Motor - https://grabcad.com/library/12v-dc-motor-350rpm-w-encoder-from-dfrobot-1
<li> MG996R Servo motor - https://grabcad.com/library/servomotor-mg996r-4
<li> Sparkfun Motor Driver - https://grabcad.com/library/sparkfun-motor-driver-dual-tb6612fng-1a-1
<li> Teensy 4.1 - https://grabcad.com/library/teensy-4-1-2
<li> RPLIDAR A1 - https://grabcad.com/library/rplidar-a1-holder-1
<li> Pixycam 2.1 - https://grabcad.com/library/cmucam-pixy-2-2
<li> LiPo Battery - https://grabcad.com/library/2s-7-4v-li-po-battery-1
<li> Grove BMI088 Gyroscope - https://grabcad.com/library/mpu6050-1
<li> Linear Voltage Regulator - https://grabcad.com/library/linear-voltage-regulators-78xx-1
<li> Prototype Board - https://grabcad.com/library/pcb-board-prototype-3x7cm-1

<br>

## Images 
<li> DC Motor - https://www.adafruit.com/product/4416
<li> Sparkfun Motor Driver - https://cdn.sparkfun.com//assets/parts/1/2/4/8/2/14450a-01.jpg
<li> MG996R Servo motor - https://www.digikey.com/htmldatasheets/production/5014637/0/0/1/media/bg1.jpg
<li> Teensy 4.1 - https://circuitpython.org/assets/images/boards/large/teensy41.jpg
<li> RPLIDAR A1 - https://www.waveshare.com/wiki/RPLIDAR_A1
<li> Pixycam 2.1 - https://pixycam.com/wp-content/uploads/2021/05/pixy2_3_result.jpg
<li> LiPo Battery - https://www.autorc.ro/16064-large_default/acumulator-lipo-gens-ace-3s-111v-2200mah-20c-mufa-xt60.jpg
<li> Grove BMI088 Gyroscope - https://files.seeedstudio.com/wiki/Grove-6-Axis_Accelerometer-Gyroscope-BMI088/img/main.jpg
<li> Linear voltage regulator - https://ro.farnell.com/productimages/standard/en_GB/GE3TO220-40.jpg

<br>

## Copyright 

Unless explicitly stated otherwise, all rights, including copyright, in the content of these files and images are owned or controlled for these purposes by Nerdvana Romania.

You may copy, download, store (in any medium), adapt, or modify the content of these Nerdvana Romania resources, provided that you properly attribute the work to Nerdvana Romania.

For any other use of Nerdvana Romania's content, please get in touch with us at office@nerdvana.ro.

© 2023 Nerdvana Romania. All rights reserved.

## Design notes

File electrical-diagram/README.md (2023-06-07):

# Electrical Diagram
The diagram was made using www.circuit-diagram.org

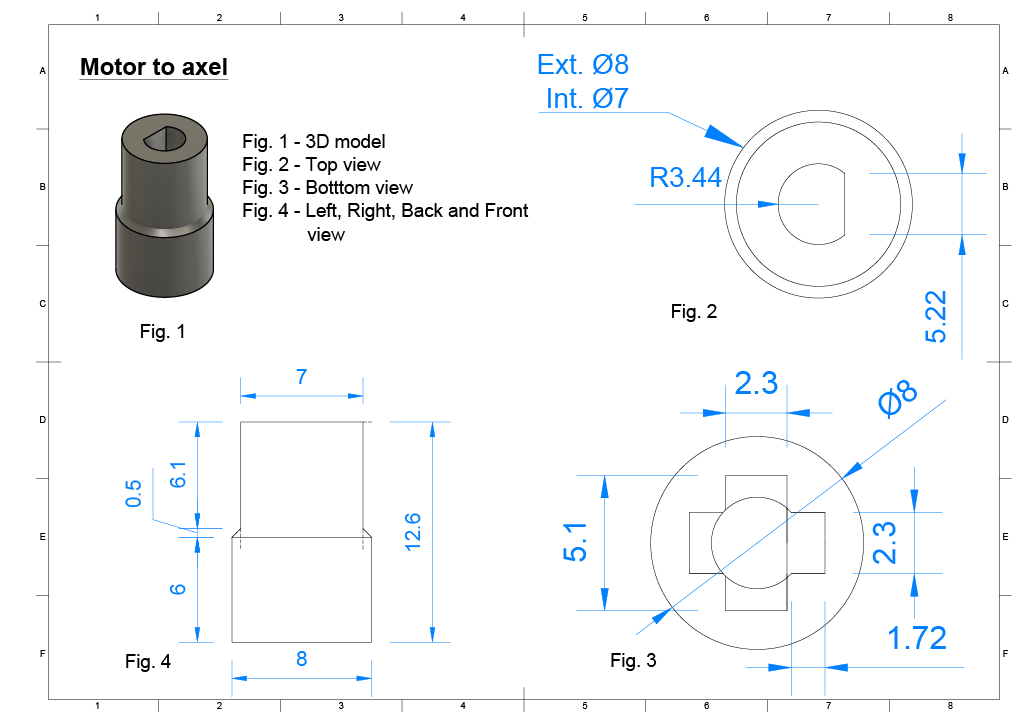
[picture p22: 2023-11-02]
images/resources/MotorToAxle.png

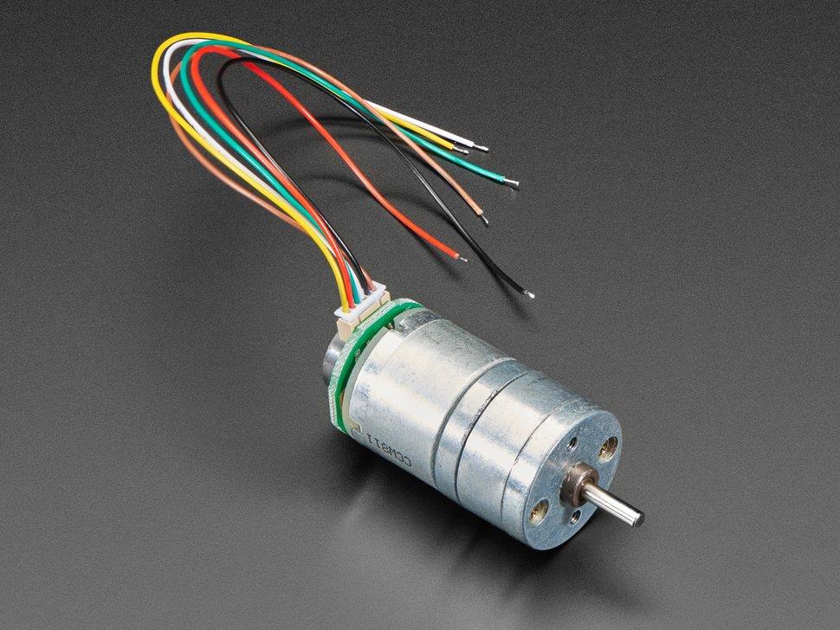
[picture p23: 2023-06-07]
images/resources/drive_motor.jpg

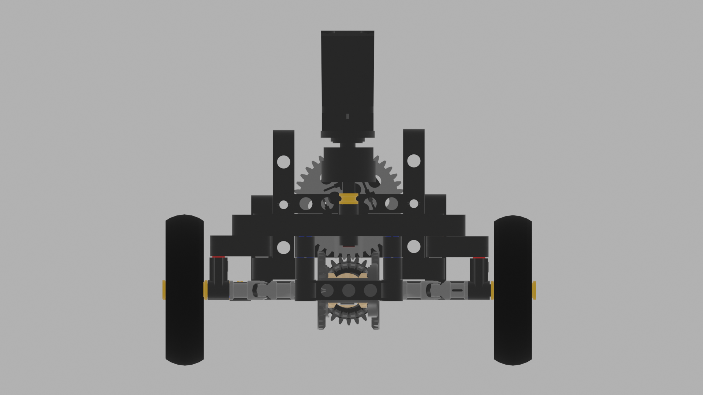
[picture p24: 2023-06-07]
images/resources/powertrain_first.png

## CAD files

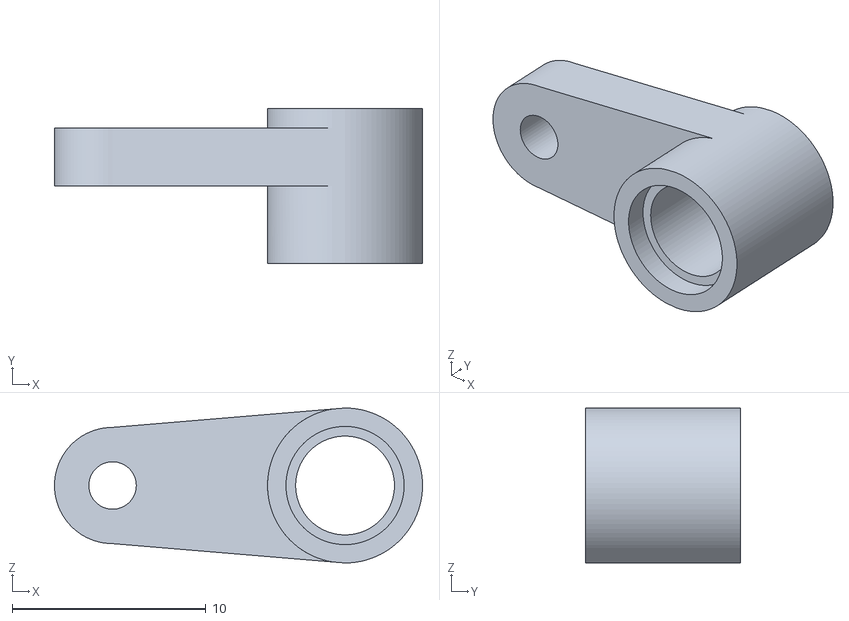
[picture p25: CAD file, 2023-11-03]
3d-models/lidar_support.stl
19.0 x 8.00 x 8.00

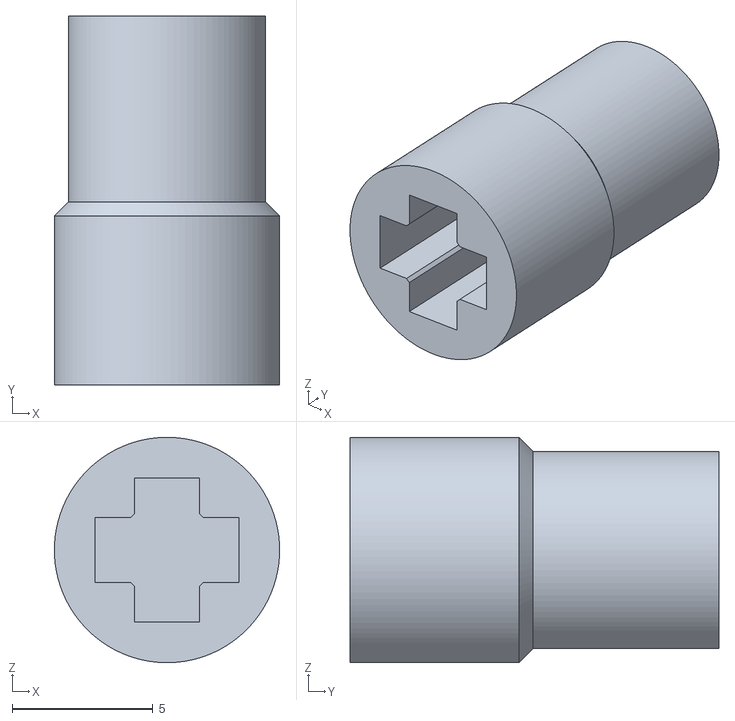
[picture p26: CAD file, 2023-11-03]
3d-models/motor_to_axle.stl
8.00 x 13.1 x 8.00

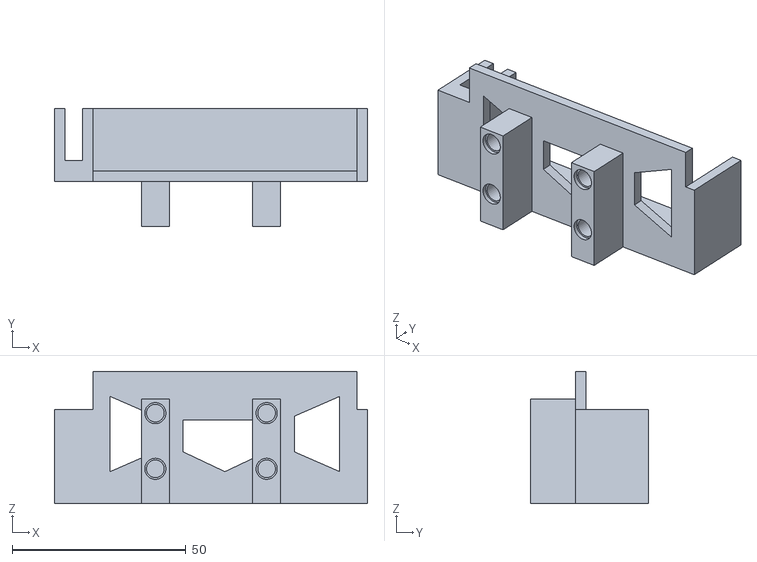
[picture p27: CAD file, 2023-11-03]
3d-models/battery_suport.stl
90.0 x 34.0 x 38.0

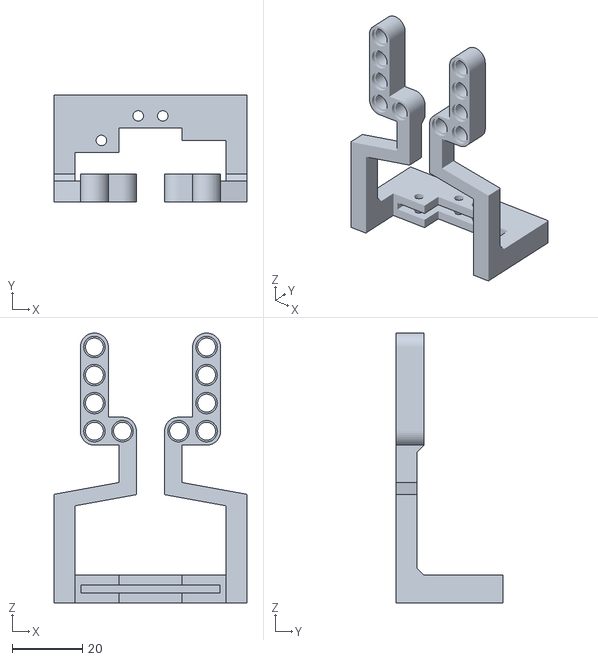
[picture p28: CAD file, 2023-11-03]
3d-models/camera_suport.stl
55.0 x 30.6 x 77.0

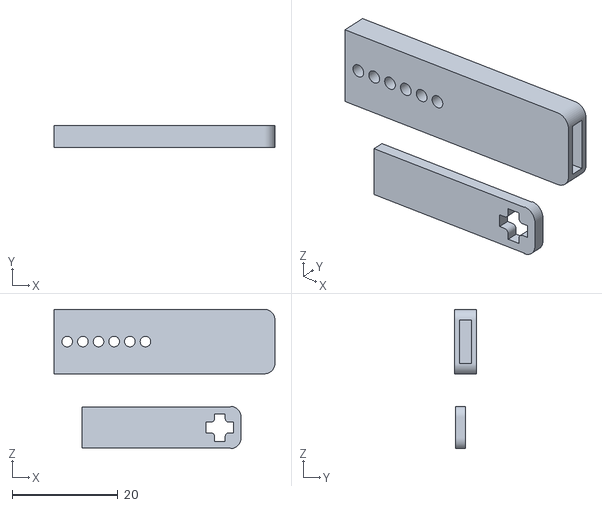
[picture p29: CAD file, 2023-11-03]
3d-models/servo_arm v1.stl
41.8 x 4.20 x 26.4

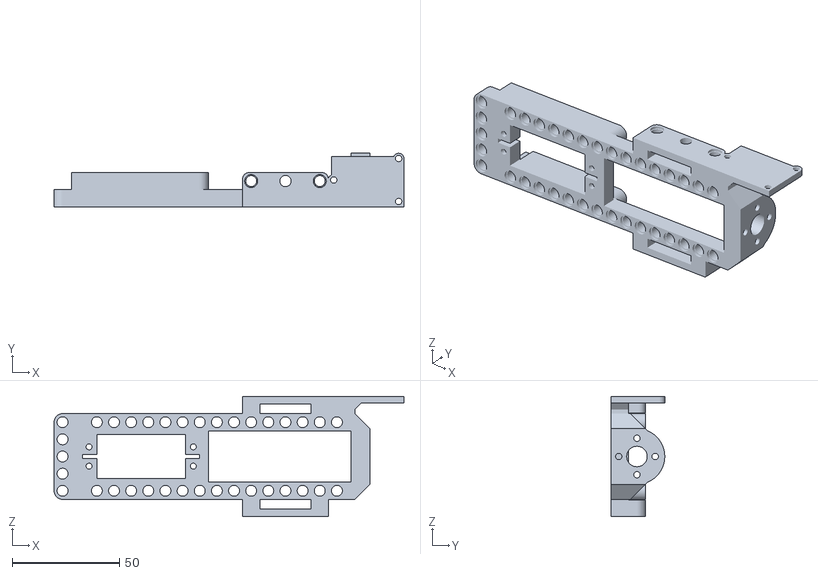
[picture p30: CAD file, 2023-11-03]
3d-models/robot_2023_fe v14.stl
163.3 x 25.0 x 56.0

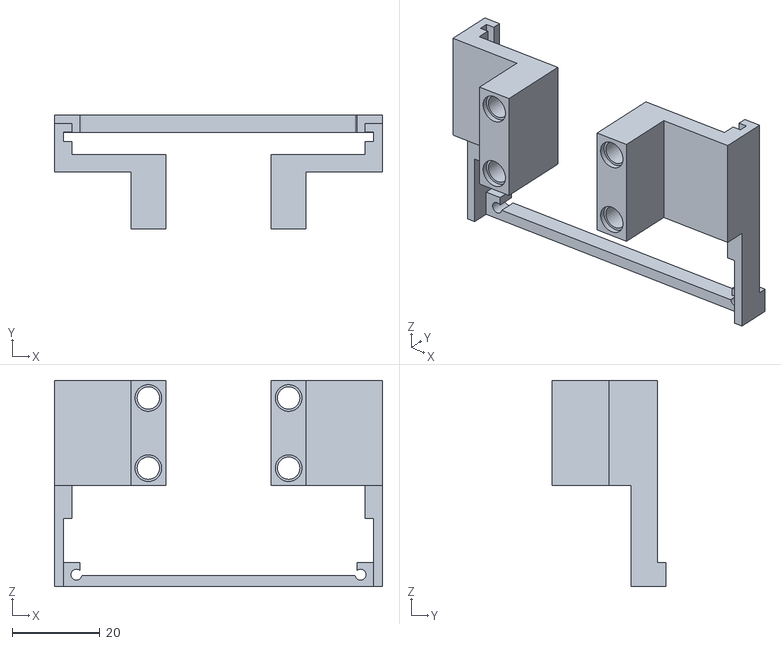
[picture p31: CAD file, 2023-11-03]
3d-models/PCB_support.stl
74.8 x 26.0 x 47.0

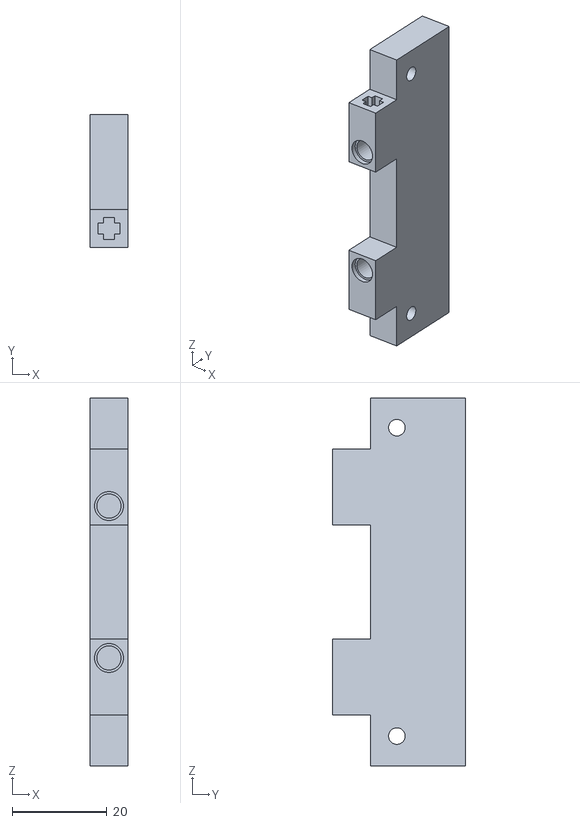
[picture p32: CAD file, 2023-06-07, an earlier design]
3d-models/old-models/suport_teensy v4.stl
8.00 x 28.0 x 77.5

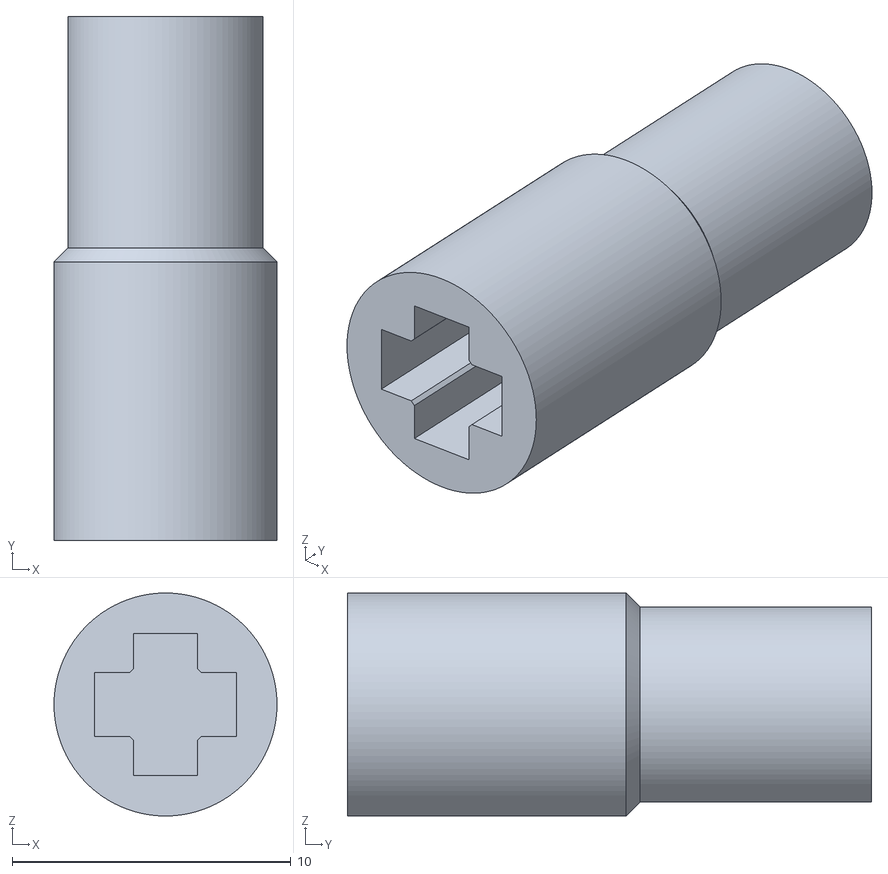
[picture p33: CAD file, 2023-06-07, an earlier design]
3d-models/old-models/gearmotor_to_axle v8.stl
8.00 x 18.8 x 8.00

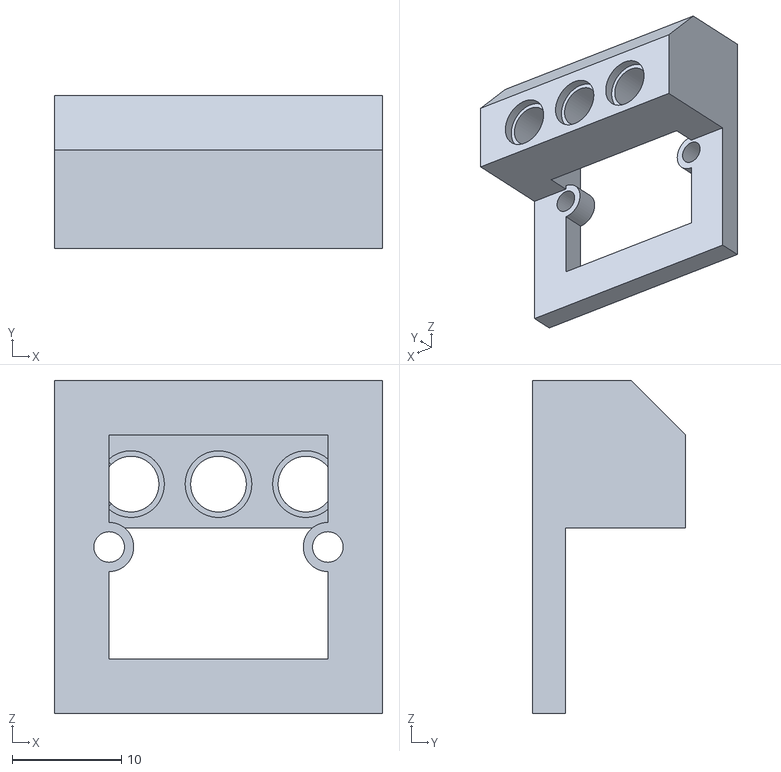
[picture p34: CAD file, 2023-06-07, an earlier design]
3d-models/old-models/lidar_to_lego v2.stl
30.0 x 14.0 x 30.5

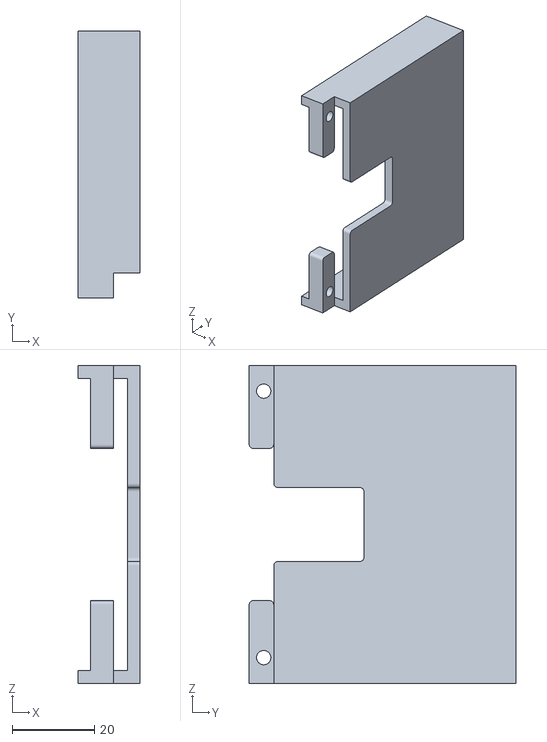
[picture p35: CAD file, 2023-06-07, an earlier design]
3d-models/old-models/pcb_back_plate v2.stl
15.1 x 65.0 x 77.5

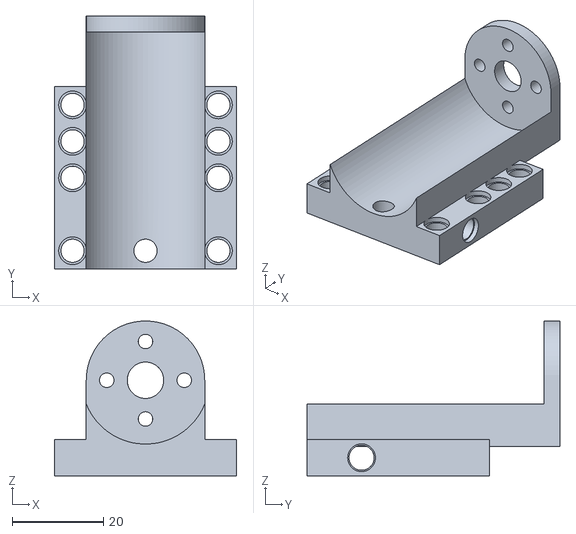
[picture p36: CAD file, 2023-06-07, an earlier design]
3d-models/old-models/GM25 GEARMOTOR Support lego v6.stl
40.0 x 55.5 x 34.0

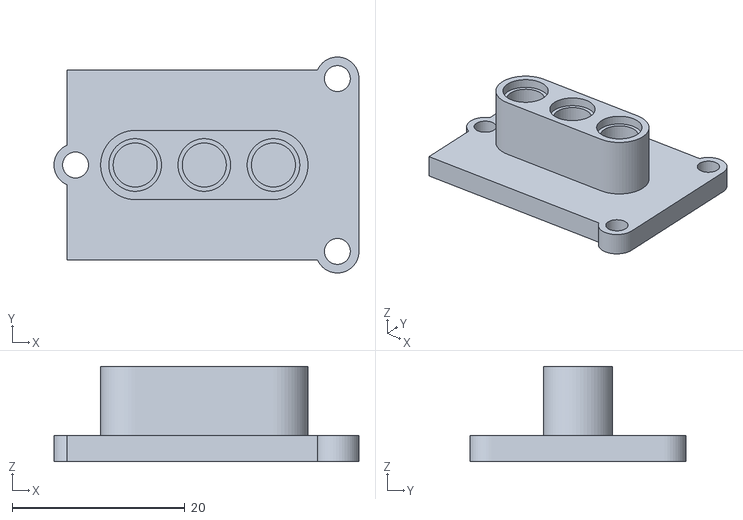
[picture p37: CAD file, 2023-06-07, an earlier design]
3d-models/old-models/grove_suport v2.stl
35.3 x 25.0 x 11.0

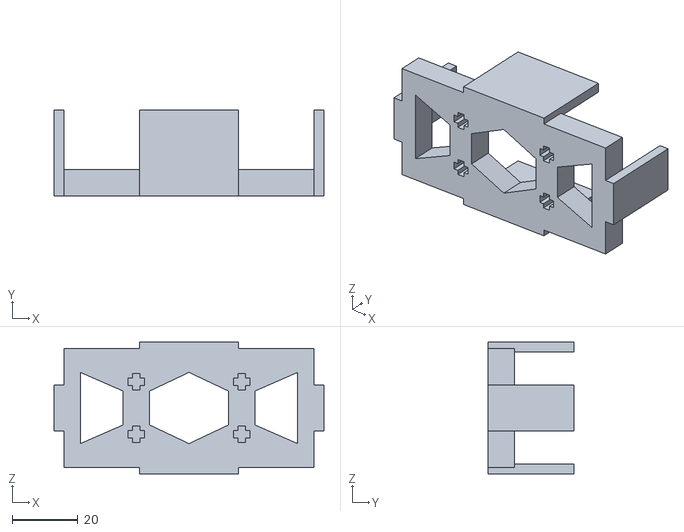
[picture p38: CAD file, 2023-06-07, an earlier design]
3d-models/old-models/Battery Support Lego v2.stl
82.0 x 26.0 x 40.0

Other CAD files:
3d-models/old-models/Pixycam lego support v8.stl
3d-models/old-models/servo_MG996R v3.stl
3d-models/old-models/MG996R_to_axle v5.stl

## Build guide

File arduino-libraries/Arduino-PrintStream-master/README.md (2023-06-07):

# Arduino-PrintStream

A simple library, that adds `std::cout`-like support for the Arduino (using the `<<`-operator).

## Example usage

```cpp
#include <PrintStream.h>
void setup() {
  Serial.begin(115200);
  Serial << "Hello, World!" << endl;

  Serial << F("Counting to 0xf in hexadecimal: ")
         << hex << noleadingzeros << showbase;
  for (int i = 0; i < 0x10; i++)
    Serial << i << ' ';
  Serial << dec << endl;

  float voltage = analogRead(A0) * 5 / 1024.0;
  Serial << F("The voltage on analog pin A0 is ") << setprecision(3) << voltage << F(" V.") << endl;
}

void loop() { }
```

## Installation

Download the library as a ZIP file, and import it into the Arduino IDE as explained [here](https://www.arduino.cc/en/guide/libraries#toc4).

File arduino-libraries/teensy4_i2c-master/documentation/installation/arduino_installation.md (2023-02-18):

# Arduino Installation
These instructions explain how to use this library with the [Arduino IDE](https://www.arduino.cc/en/software).

1. [Download](https://github.com/Richard-Gemmell/teensy4_i2c/archive/refs/heads/master.zip)
the zip of the master branch.
1. Install teensy4_i2c as a "custom library" using the [standard Arduino instructions](https://www.arduino.cc/en/Guide/Libraries#importing-a-zip-library)

Once you've installed the library you can pick one of the examples
from the bottom of the "File | Examples" drop menu.

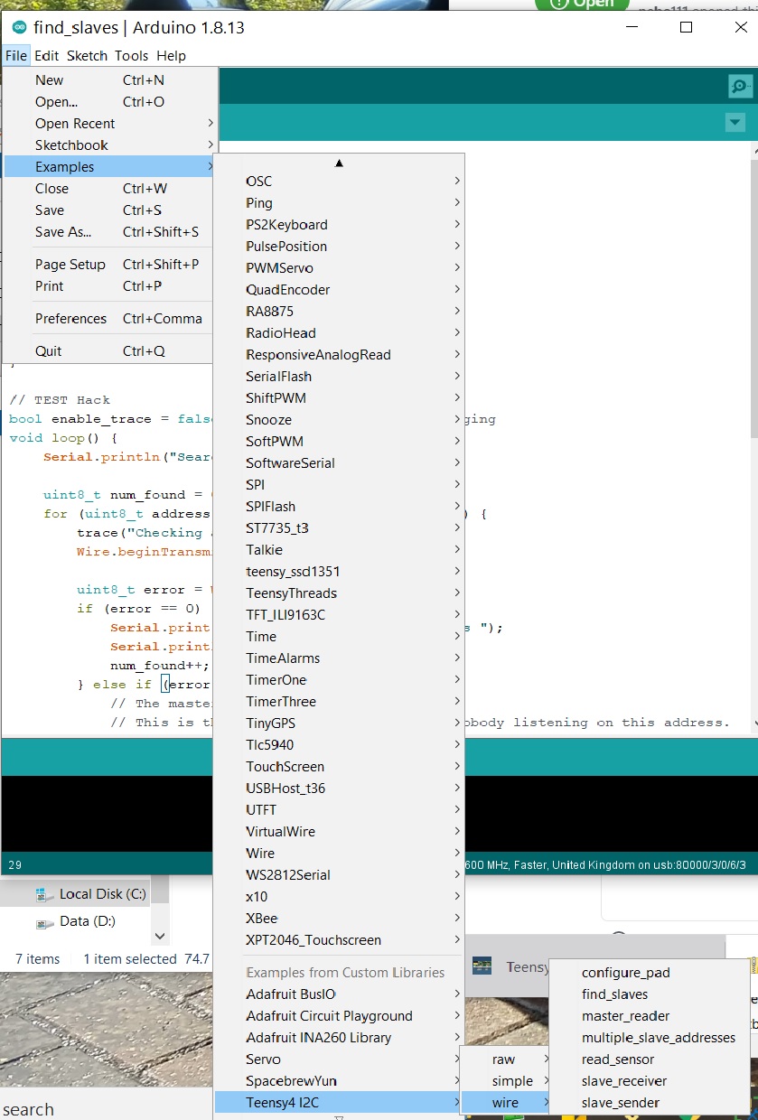
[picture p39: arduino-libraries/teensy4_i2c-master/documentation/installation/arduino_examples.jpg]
pick_example


The "wire | find_slaves" example should work without changes.

# Using Another Branch 
See [Getting Code out of GitHub](github_help.md) if you want to
install a different branch. (You wouldn't normally do this unless
you're trying out a bug fix or pre-release version.)

# Troubleshooting
Arduino should add the library to your "Sketchbook location" directory.
It will include the entire contents of the teensy4_i2c project.

In my case this directory is
`C:\Users\Richard\Documents\Arduino\libraries`.

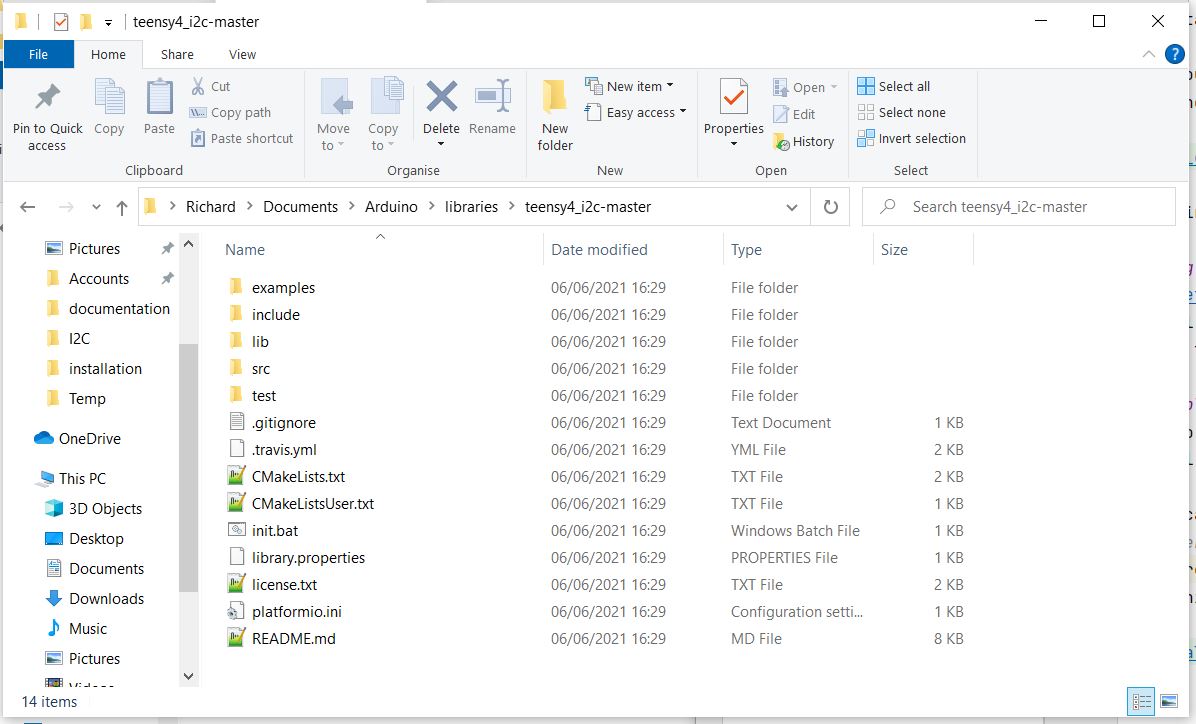
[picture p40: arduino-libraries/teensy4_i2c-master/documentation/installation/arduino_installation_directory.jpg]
installation


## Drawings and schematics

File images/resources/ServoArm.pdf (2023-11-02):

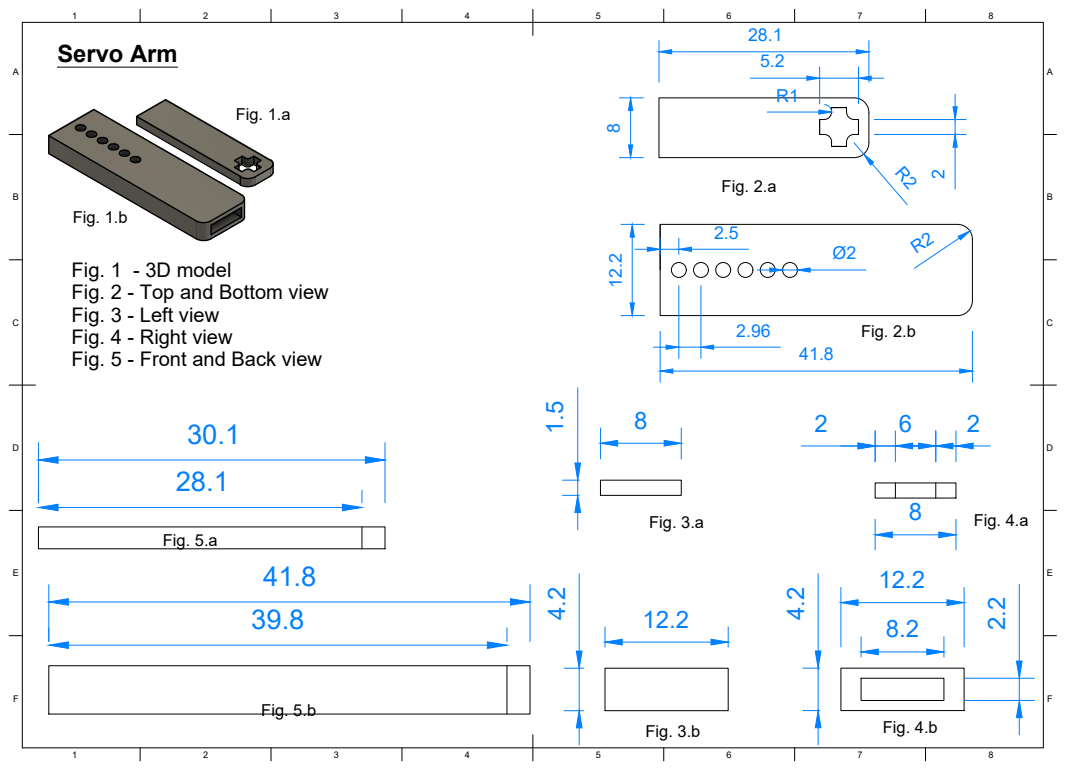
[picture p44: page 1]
8 BCDEF; ABCDEF; Fig. 1.a; Fig. 1.b; Fig. 2.a; Fig. 2.b; Fig. 3.a; Fig. 4.a; Fig. 3.b; Fig. 4.b; Fig. 5.a; Fig. 5.b; Servo Arm

Fig. 1 - 3D model
Fig. 2 - Top and Bottom view
Fig. 3 - Left view
Fig. 4 - Right view
Fig. 5 - Front and Back view

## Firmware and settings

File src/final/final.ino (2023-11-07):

#include <math.h>
#include <string.h>
#include <PrintStream.h>

#include <Servo.h>
#include <Wire.h>
#include "BMI088.h"
#include <Encoder.h>
#include <Servo.h>
#include <Pixy2I2C.h>

#include <SD.h>
#include <SPI.h>

// SD Card
#define chipSelect BUILTIN_SDCARD
// Camera
#define CAMERA_FPS 30


// SD card
const long sd_interval = 20;
double sd_last_write_time = 0;
char sd_filename[100];
String data_string = "";
bool debug = true;



#define Vector Point


// ============================= GEOMETRIC OBJECTS =============================

struct Point {
  int16_t x;
  int16_t y;

  Point()
    : x(0), y(0) {}
  Point(int16_t x, int16_t y)
    : x(x), y(y) {}
};

struct Angle {
  double dist;
  double ang;

  // Default constructor
  Angle()
    : dist(0), ang(0) {}

  // Parameterized constructor
  Angle(double dist, double ang)
    : dist(dist), ang(ang) {}
};

struct Cube {
  int color;  // -1 - green, 1 - red
  int x, y;
  int w, h;
  int index;
} corner_cube, cube;


const int MAX_CNT_POINTS = 2000;

Point points[MAX_CNT_POINTS];
int cntPoints = 0;

Angle angles[MAX_CNT_POINTS];

double gx, gy, gz;

int current_motor_speed = 100;
int motor_speed = 80;

#define FRONT 0
#define RIGHT 1
#define BACK 2
#define LEFT 3

#define GREEN -1
#define RED 1

#define WALL_NR 4
int wall_dist[WALL_NR];
double slopes[WALL_NR];
int old_wall_dist[WALL_NR];
int wall_inv[WALL_NR] = { BACK, LEFT, FRONT, RIGHT };

// ============================= SETUP =============================


int direction = 1;
int side_wall = LEFT;
double current_angle = 0;

void setup() {
  Serial.begin(115200);

  servo_setup();

  SD_setup();
  camera_setup(true);

  gyro_setup(true);
  Serial.println("Finished Gyro");

  lidarSetup();

  Serial.println("Finised seting up the lidar");

  motor_driver_setup();

  double start_lidar_time = millis();

  while (millis() - start_lidar_time < 1000) {
    lidarRead();
    read_gyro(false);
  }

  while(digitalRead(BUTTON_PIN) == 1) {
    lidarRead();
    read_gyro(false);
  }

  motor_start(motor_speed);
}

// ============================= LOOP =============================

double d1, d2, d3, d4;  //left front right back

long last_gyro_read;
long gyro_read_interval = 1;

long long numberPoints = 0;

double last_time_pid = 0;

double flag_time = 0;
int flagg = 0;

const double camera_interval = (1000 / CAMERA_FPS);
double last_camera_read = 0;
int cube_color = 0;  // -1 green, 0 none, 1 red

#define SECTION 0
#define ROTATE 1
#define GO_SECTION 2
#define AVOID_CUBE 3
#define PASS_CUBE 4
#define PASS_LAST_CUBE 5



#define STOP 10

int CASE = SECTION;
int turns = 0;
int pid_case = 0;

int last_time1 = millis();
int cnt1 = 0;
int loop_cnt = 0;

bool gyro_flag, accel_flag;

double dist_to_cube = 0;
double last_dist_to_cube = 0;
double dist_cube_wall = 0;
double last_cube_y = 0;

double last_read_cube = millis();

#define SECTION_NR 4
#define POSITION_NR 2

// -1 green, 0 none, 1 red
int cube_colors[SECTION_NR][POSITION_NR] = { { -1, 1 }, { -1, -1 }, { 1, 0 }, { -1, 0 } };

int section = 0;
// int current_cube_color = get_cube(section, 0);

int goal_distance = 0;

int last_cube_color = 0;

double last_avoid_cube_time = 0;

double last_rotate = 0;
double rotate_timeout = 2500;
double last_turn_ok = 0;
double xa = 0;
double ya = 0;

double kp = 0.0018;  //0.0013;
double ki = 0;
double kd = 0.003;
double pid_error = 1, pid_last_error = 0;

double kp_gyro = 0.04;
double ki_gyro = 0;
double kd_gyro = 0.25;
double pid_error_gyro, pid_last_error_gyro = 0;

double ang = 0;

bool flag = 0;

int turn_ok = 1;

int final_cube_color = 0;
int final_cube_pos = 0;
int final_cube_turn = 0;

int cube_section_cnt = 0;

void loop() {
  lidarRead();
  read_gyro(false);
  read_camera(true);

  if (millis() - last_gyro_read > 10) {
    Serial << " C: " << CASE << " f: " << wall_dist[FRONT] << " r: " << wall_dist[RIGHT]
           << " b: " << wall_dist[BACK] << " l: " << wall_dist[LEFT] << " " << gx << " " << pid_error << " " 
           << pid_error_gyro << " " << dist_to_cube << " " << last_dist_to_cube << " " << goal_distance << " " 
           << xa << " " << ya << " " << last_cube_y << " " << cube_color << "\n";
    last_gyro_read = millis();
    writeSD();
  }

  if(turns == 12 && millis() - last_rotate > rotate_timeout && wall_dist[BACK] > 1100 && wall_dist[BACK] < 2000 && (wall_dist[LEFT] + wall_dist[RIGHT]) < 1200) {
    CASE = STOP;
  }

  if(direction == 0 && (wall_dist[LEFT] + wall_dist[RIGHT]) > 1200) {
    if(wall_dist[LEFT] > wall_dist[RIGHT]) {
      direction = 1;
      side_wall = LEFT;
    } else {
      direction = -1;
      side_wall = RIGHT;
      current_angle = -5;
    }
  }

  switch (CASE) {

    case SECTION:
      {
        if(turn_ok && wall_dist[FRONT] && wall_dist[FRONT] < 700  && millis() - last_rotate > rotate_timeout) {
          turns++;
          last_rotate = millis();
          last_cube_color = 0;
          last_dist_to_cube = 0;
          flag = 0;
          cube_section_cnt = 0;
          if (wall_dist[side_wall] > 550)
            CASE = ROTATE;
          else
            current_angle += direction * 90;
          
          // CASE = STOP;
        } else if (last_dist_to_cube && cube_color != last_cube_color && cube_color != 0 && wall_dist[BACK] < 1800) {

          // data_string += "a intrat sloboz, cube_color: " + String(cube_color) + ", last_cube_color " + String(last_cube_color) + '\n';

          move_servo(cube_color * 1);

          if (cube_color == GREEN) {
            if(direction == 1)
              goal_distance = 250 + (wall_dist[side_wall] - 230) / 6;
            else
              goal_distance = 850 - (1000 - wall_dist[side_wall]) / 6;
          } else {
            if(direction == 1)
              goal_distance = 770 - (1000 - wall_dist[side_wall]) / 5;
            else
              goal_distance = 270 + (wall_dist[side_wall] - 200) / 5;
          }

          last_cube_color = cube_color;
          // save last cube 

          cube_section_cnt++;

          if(turns == 3) {
            final_cube_color = last_cube_color;
            final_cube_pos = cube_section_cnt;
            final_cube_turn = turns;
          } 
          if(turns == 4) {
            if(last_cube_y < 1700) {
              final_cube_color = last_cube_color;
              final_cube_pos = cube_section_cnt;
              final_cube_turn = turns;
            }
          }
          
          CASE = AVOID_CUBE;
        } else {

          if(millis() - last_turn_ok > rotate_timeout && (wall_dist[BACK] > 1850 || (wall_dist[LEFT] + wall_dist[RIGHT]) > 1200) && !turn_ok) {
            turn_ok = 1;
            last_turn_ok = millis();
          }
          pid_error_gyro = ((current_angle) - gx) * kp_gyro + (pid_error_gyro - pid_last_error_gyro) * kd_gyro;
          pid_last_error_gyro = pid_error_gyro;

          move_servo(pid_error_gyro);
        }
        break;
      }

    case AVOID_CUBE:
      {
        if (last_cube_color == GREEN && ((wall_dist[side_wall] < goal_distance && direction == 1) || (wall_dist[side_wall] > goal_distance && direction == -1))  || 
              last_cube_color == RED && ((wall_dist[side_wall] > goal_distance && direction == 1) || (wall_dist[side_wall] < goal_distance && direction == -1)) && 
                (wall_dist[LEFT] + wall_dist[RIGHT]) > 800) {
          CASE = PASS_CUBE;
        } else {
          pid_error_gyro = ((current_angle + last_cube_color * 55) - gx) * kp_gyro + (pid_error_gyro - pid_last_error_gyro) * kd_gyro;
          pid_last_error_gyro = pid_error_gyro;

          move_servo(pid_error_gyro);
        }
        break;
      }

    case PASS_CUBE:
      {
        if (wall_dist[BACK] > last_cube_y + 200 && (wall_dist[FRONT] + wall_dist[BACK]) < 3400) {
          last_dist_to_cube = 0;
          if(final_cube_color == 1 && final_cube_turn % 4 == turns % 4 && turns > 5 && final_cube_pos == cube_section_cnt)
            CASE = PASS_LAST_CUBE;
          else
            CASE = SECTION;
        } else {
          pid_error_gyro = (current_angle - gx) * kp_gyro + (pid_error_gyro - pid_last_error_gyro) * kd_gyro;
          pid_last_error_gyro = pid_error_gyro;

          move_servo(pid_error_gyro);
        }
        break;
      }

    case ROTATE:
      {
        if (abs((current_angle - direction * 270) - gx) < 5) {
          current_angle -= direction * 270;
          last_rotate = millis();
          CASE = SECTION;
        } else if ((wall_dist[side_wall] > 500 || wall_dist[FRONT] > 450) && (wall_dist[side_wall] > 450 || wall_dist[FRONT] > 250) && flag == 0) {
          ang = myacos((wall_dist[FRONT] - 450) / sqrt((wall_dist[FRONT] - 450) * (wall_dist[FRONT] - 450) + (wall_dist[side_wall] - 500) * (wall_dist[side_wall] - 500)));

          pid_error_gyro = ((current_angle - direction * ang) - gx) * kp_gyro + (pid_error_gyro - pid_last_error_gyro) * kd_gyro;
          pid_last_error_gyro = pid_error_gyro;

          move_servo(pid_error_gyro);
        } else {
          flag = 1;
          pid_error_gyro = ((current_angle - direction * 270) - gx) * kp_gyro + (pid_error_gyro - pid_last_error_gyro) * kd_gyro;
          pid_last_error_gyro = pid_error_gyro;

          move_servo(pid_error_gyro);
        }
        break;
      }

    case PASS_LAST_CUBE: {
      if(wall_dist[FRONT] && wall_dist[FRONT] < 500) {
        current_angle -= 180;
        direction *= -1;
        if(side_wall == LEFT)
          side_wall = RIGHT;
        else
          side_wall = LEFT;
        last_rotate = millis();
        last_cube_color = 0;
        last_dist_to_cube = 0;
        flag = 0;
        cube_section_cnt = 0;
        turns++;
        CASE = SECTION;
      } else {
        pid_error_gyro = (current_angle - gx) * kp_gyro + (pid_error_gyro - pid_last_error_gyro) * kd_gyro;
        pid_last_error_gyro = pid_error_gyro;

        move_servo(pid_error_gyro);
      }
      break;
    }
    
    case STOP:
      {
        lidarMotorWrite(0);
        move_servo(0);
        motor_start(-10);
        Serial.println("Stop case");
        break;
      }

    default:
      {
        break;
      }
  }
}

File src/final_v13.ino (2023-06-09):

#include <math.h>
#include <string.h>
#include <PrintStream.h>

#include <Servo.h>
#include <Wire.h>
#include <Pixy2I2C.h>
#include "BMI088.h"
#include <Encoder.h>
#include <U8g2lib.h>
#include "Ultrasonic.h"

#include <SD.h>
#include <SPI.h>


///====================///
///      Defines       ///
///====================///


// Motor driver
#define PWM1 7
#define AIN1 9
#define AIN2 8

// Motor Encoder
#define ENCODER_PIN1 5
#define ENCODER_PIN2 4

// Servo
#define SERVO_PIN 6

// Camera
#define CAMERA_FPS 60

// Distance sensors
#define FRONT_SENSOR_PIN 2
#define LEFT_SENSOR_PIN 1
#define RIGHT_SENSOR_PIN 0

// Gyro sensor
#define GYRO_SAMPLE_SIZE 1
#define DRIFT_TEST_TIME 10

// Led
#define LED_PIN LED_BUILTIN

// SD Card
#define chipSelect BUILTIN_SDCARD

//BUTTON
#define BUTTON_PIN 32

/// Use parts defines
#define USE_MOTOR_DRIVER
#define USE_MOTOR_ENCODER
#define USE_SERVO
#define USE_CAMERA
#define USE_DISTANCE_SENSORS
#define USE_GYRO
#define USE_LED
#define USE_DISPLAY
#define USE_SD
// #define USE_BUTTON
#define USE_MOTOR_SAFETY

/// State machine cases
#define CUBE_PID_CASE 0
#define AVOID_CASE 1
#define TURN_CASE 2
#define GYRO_PID_CASE 3
#define TURN_TO_CENTER_CASE 4
#define GO_STRAIGHT_CASE 5
#define FINISH_CASE 6


///====================///
///   Initialization   ///
///====================///


// Motor encoder
Encoder myEnc(ENCODER_PIN1, ENCODER_PIN2);

// Servo
Servo servo;

// Camera
Pixy2I2C pixy_left;
Pixy2I2C pixy_right;

// Distance sensors
Ultrasonic ultrasonic_front(FRONT_SENSOR_PIN);
Ultrasonic ultrasonic_left(LEFT_SENSOR_PIN);
Ultrasonic ultrasonic_right(RIGHT_SENSOR_PIN);

// Gyro sensor
Bmi088 bmi(Wire, 0x19, 0x69);

// Display
U8G2_SSD1306_128X64_ALT0_F_HW_I2C u8g2(U8G2_R0, /* reset=*/U8X8_PIN_NONE);


///====================///
///      Variables     ///
///====================///

// Motor driver
int motor_speed = 50;
int medium_motor_speed = 50;
int current_motor_speed = 0;
double motor_speed_interval = 150;
double last_time_motor_speed = 0;
double last_motor_encoder = 0;

unsigned long safety_timeout = 1500;
unsigned long last_safety_time = 0;
int last_motor_enc = -999;

// Servo
double delay_angle = 165 / 60;
double servo_correction = -0.15;

// Camera
const double camera_fps = (1.0 / CAMERA_FPS) * 1000.0;
double camera_last_fps = 0;
int min_area_cube = 0;
int max_area_cube = 25000;

const int camera_w = 316;
const int camera_h = 208;
const int camera_joint_width = 72;

const int image_w = camera_w * 2 - camera_joint_width;
const int image_h = camera_h;

const int sig_to_col[] = { 0, 1, -1 };  // 0 - none, -1 - green, 1 - red

int cube_array_size = 0;

struct Cube {
  int color;  // -1 - green, 1 - red
  int x, y;
  int w, h;
  int index;
} cube_array[10], corner_cube, cube;

int ignore_index = -10000000;

// Distance sensors
int left_sensor_cm = 0, right_sensor_cm = 0, front_sensor_cm = 0;
unsigned long last_time_front_sensor = 0, last_time_left_sensor = 0, last_time_right_sensor = 0;

// Gyro sensor
double gx, gy, gz;
unsigned long gyro_last_read_time = 0;
double drifts_x, drifts_y, drifts_z;

// Led
int led_state = LOW;                  // led_state used to set the LED
const long led_interval = 1000;       // led_interval at which to blink (milliseconds)
unsigned long led_previous_time = 0;  // will store last time LED was updated

// Display
const unsigned long display_print_interval = 200;
unsigned long display_last_print_time = 0;

// SD card
const long sd_interval = 5;
long sd_last_write_time = 0;
char sd_filename[100];
String data_string = "";

// Setup
bool init_error = false;
bool init_sensors_error = false;
bool init_gyro_error = false;
bool init_display_error = false;
bool init_sd_error = false;

// Main loop
unsigned long loop_start_time = 0;
unsigned long loop_iteration = 0;
unsigned long loop_temp_iteration = 0;
unsigned long loop_last_time = 0;
long loop_freq = 0;

bool debug = false;

unsigned long last_side_read = 0;
unsigned long side_read_timeout = 250;
int distance_between_walls = 130;

int turn_direction = 0;
int actual_cube_nr;

///====================///
///     Functions      ///
///====================///


float clamp(float val, float small, float big) {
  return max(small, min(val, big));
}


/// Display functions

void display_print(const char *s) {
#ifdef USE_DISPLAY
  u8g2.clearBuffer();
  u8g2.drawStr(30, 20, s);
  u8g2.sendBuffer();
#endif  // USE_DISPLAY
}

void display_print(const char *s1, const char *s2) {
#ifdef USE_DISPLAY
  u8g2.clearBuffer();
  u8g2.drawStr(30, 15, s1);
  u8g2.drawStr(30, 25, s2);
  u8g2.sendBuffer();
#endif  // USE_DISPLAY
}

void display_print(const double n, const char *sufix = "") {
#ifdef USE_DISPLAY
  char s[100];
  itoa(n, s, 10);
  strcat(s, sufix);

  u8g2.clearBuffer();
  u8g2.drawStr(30, 20, s);
  u8g2.sendBuffer();
#endif  // USE_DISPLAY
}


void display_print(const double a, const double b) {
#ifdef USE_DISPLAY
  char s1[100], s2[100];
  itoa(a, s1, 10);
  itoa(b, s2, 10);

  u8g2.clearBuffer();
  u8g2.drawStr(30, 15, s1);
  u8g2.drawStr(30, 25, s2);
  u8g2.sendBuffer();
#endif  // USE_DISPLAY
}


/// Motor functions

void motor_start(int speed) {
  current_motor_speed = speed;

  int out = abs(speed) * 2.55;  // Convert speed to PWM value (0 to 255)
  if (speed >= 0) {             // Forward direction
    digitalWrite(AIN1, HIGH);
    digitalWrite(AIN2, LOW);
  } else {  // Reverse direction
    digitalWrite(AIN1, LOW);
    digitalWrite(AIN2, HIGH);
  }
  analogWrite(PWM1, out);
}

void motor_stop() {
  motor_start(-1);
  current_motor_speed = 0;
}

long read_motor_encoder() {
  return (double)myEnc.read() / 47.74;
}

/// Servo functions

void move_servo(double angle) {
  angle = clamp(angle + servo_correction, -1, 1);

  double angle_deg = 90 + angle * 90.0;  // Convert angle to degrees (0 to 180)
  angle_deg = clamp(angle_deg, 0, 180);
  servo.write(angle_deg);
}


/// camera functions

int sort(const void *cmp1, const void *cmp2) {
  Cube a = *((Cube *)cmp1);
  Cube b = *((Cube *)cmp2);

  return b.x - a.x;
}
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

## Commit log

2023-02-18 Camera/Sensors
    Camera and Sensors files and libraries
2023-02-23 Encoder code
2023-06-07 Multiple lidars, incorporating everything in one program
2023-06-07 Github documentation - continuation
    [Battery Support Lego v2.stl, GM25 GEARMOTOR Support lego v6.stl, MG996R_to_axle v5.stl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]
2023-06-09 Changes for the National
    Modified code,
    Modified circuit diagram,
    Added team photo,
    Added performance video,
    Added information in the README
2023-10-31 Lidar code changes
2023-10-31 Lidar circuit
2023-11-02 Mobility Management, Electrical Components & Power and Sens Management
2023-11-03 3D models
    [PCB_support.stl, battery_suport.stl, camera_suport.stl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]
2023-11-07 This commit includes changes that were meant to be pushed on 5 November, but due to issues with uploading, are being committed today.
    [3_gyro.ino, 4_lidar.ino, 5_motor_functions.ino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]
